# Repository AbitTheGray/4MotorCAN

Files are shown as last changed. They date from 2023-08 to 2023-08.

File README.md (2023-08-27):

# 3D Printer 4-Motor Board (CAN-bus Device)

This is a hobby project to create 3D Printer board to allow either control of all 4 motors (XYZ + Extruder) or 4 motors per axis.

The brain is [RP2040](https://www.raspberrypi.com/products/rp2040/) (can be flashed using USB-C connector) and has [TMC5160](https://www.trinamic.com/products/integrated-circuits/details/tmc5160/) as its muscle.
All the power and commands are provided by [CAN bus](https://en.wikipedia.org/wiki/CAN_bus) [Molex Micro-Fit 3.0 connector](https://www.molex.com/en-us/products/connectors/wire-to-board-connectors/micro-fit-connectors).
If you do not want to use CAN bus, you must provide 24V and GND on the connector and connect USB-C to your controller.

I have tried putting as many notes into the schematic as possible.
Buck converters and LDOs have their voltage limits close to the input pins (those are recommended limits, not absolute ones).

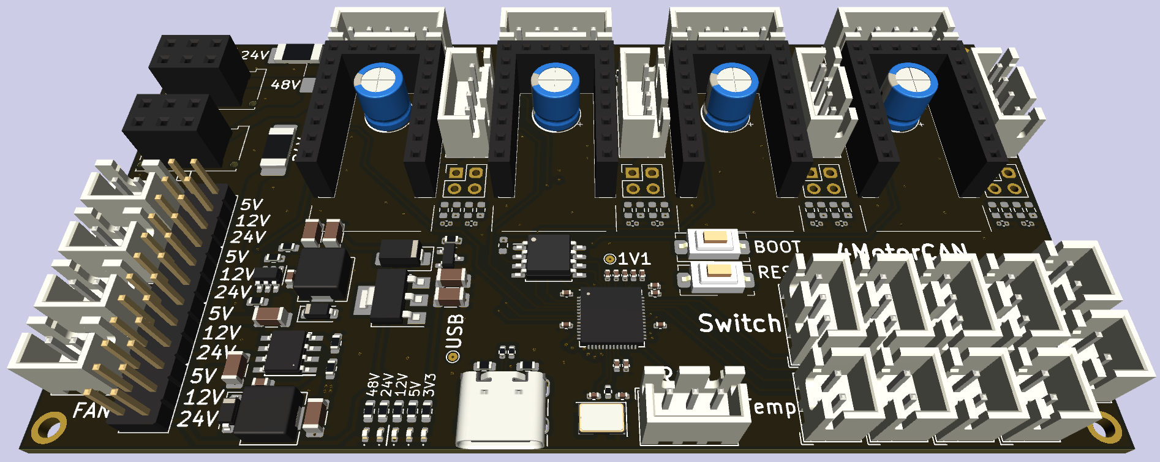
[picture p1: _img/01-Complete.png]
Fully-assembled PCB


*[Molex Micro-Fit 3.0](https://www.molex.com/en-us/products/connectors/wire-to-board-connectors/micro-fit-connectors) connectors are on the preview shown as 2x03 2.54mm/0.1" Pin Socket due to a missing 3D model.

## Features

- [CAN bus](https://en.wikipedia.org/wiki/CAN_bus) with power
  - 24V + 48V passthrough (48V optional, choose correct fuse orientation)
  - 5V signal
- 4x [TMC5160](https://www.trinamic.com/products/integrated-circuits/details/tmc5160/) to control motors (slotted PCB)
  - Encoder connector
  - Step LED (shows every step of the motor)
  - Optional direction switched (input, see TMC5160 documentation)
- 4x Limit Switch (endstop)
- RGB header (5V but signal is 3.3V)
- 4x 2pin Temperature sensor (resistor)
- 4x 2pin Fan control (5V / 12V / 24V) with 250mA fuse
- 2x Heating enable ("trigger", cannot power the heating)

### Warnings
- **This project was not yet tested. Use at your own risk.**
- This project uses RP2040 as if it was a 5V microcontroller.
  RP2040 is not officially 5V-tolerant but is reported by users to be able to process 5V input.
  And 3V output is 60% of 5V which should be enough for HIGH digital value of 5V devices.
- There is no overvoltage protection, do not turn axis motors too fast (manually)
  - Fan connectors have over-current protection (resettable fuse) in case of short circuit, but it will stop them from working
- Each motor has 3A max (total 12A) but [Molex Micro-Fit 3.0 connector](https://www.molex.com/en-us/products/connectors/wire-to-board-connectors/micro-fit-connectors) is rated only for 8.5A / 10.5A (depending on your source-of-truth) leaving only 2.125A / 2.625A per motor
    - This current limit is for the whole [CAN bus](https://en.wikipedia.org/wiki/CAN_bus)! The limit is least-rated connector in the network
    - [JST XH connectors](https://www.jst.com/products/crimp-style-connectors-wire-to-board-type/xh-connector/) should not esceed 3A.
- You should not power any heating through [CAN bus](https://en.wikipedia.org/wiki/CAN_bus) as power consumption can exceed safe limits for those connectors (and wires).

Keep in mind any current/temperature limits can be lower for higher-temperature environments (like fully boxed-in 3D printer).

## Limits and Power Consumption

| Component | Expected Max Current | Max Temperature |
|---|---|---|
| RP2040 (microcontroller) | 50 mA | 85 °C |
| W25Q128JVS (flash) | 4 mA | 85 °C (105 °C)  |
| TMC5160 (motor driver) | | 125 °C |
| Stepper motor | 3A (x4) | |

## Usage

Following usages are all theoretical based on hardware capabilities, none have been tested.

In case you do not want to use the 3mm pitch Molex connector for power, you can use the 3 pads in top-left corner to solder your wires directly to the PCB.
This is not recommended as it will usually skip fuse for motors (unless you use 24V for motors using `F103`).

### 3D Printer Board

This board can be used as a main 3D printer board as it has everything required for a basic printer (4 motors, limit switches, temperature sensors, heating triggers).

### CAN/USB Device

This device can be controlled using either [CAN bus](https://en.wikipedia.org/wiki/CAN_bus) or USB.
Having 4 motors and several input/output connectors, you can control most/all of the 3D printer from single CAN device.
In case of multiple motors per axis, you may need multiple devices (this board was primarily designed to control 4 Z-axis motors using single controller over CAN).

## Fabrication

DNP (Do Not Place/Populate) symbols are also removed from "Component Position" output.
The same applies to all connectors as those are not recommended/possible for automatic soldering.

You can save some money by replacing `R602`+`D601` by `R601` (and equivalent for `R701`,`R801` and `R901`) and omitting `R101`-`R105` and `D101`-`D105` (power indication LEDs).

### Problems

- No equivalent for `C201`/`C202` currently available
- No THT connectors in Component Placement files
  - 10x 2pin JST XH
  - 5x 3pin JST XH
  - 4x 4pin JST XH
  - 4x 5pin JST XH
  - 2x [Molex Micro-Fit 3.0 connector](https://www.molex.com/en-us/products/connectors/wire-to-board-connectors/micro-fit-connectors)
  - 2x12 2.54cm/0.1" Pin Header
  - 4x 4pin 2.54cm/0.1" Pin Header
  - 8x 8pin 2.54cm/0.1" Pin Header

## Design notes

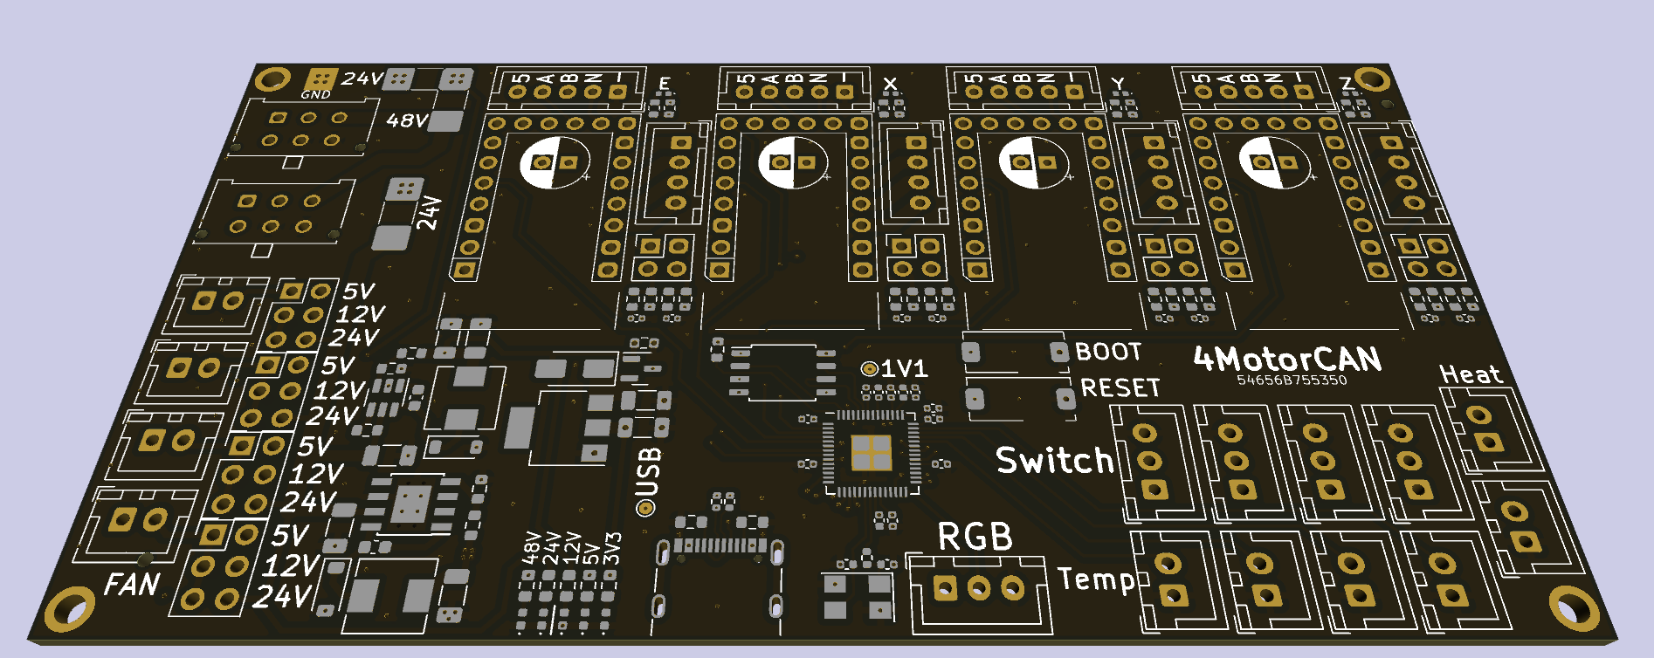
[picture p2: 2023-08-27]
_img/03-PCB.png

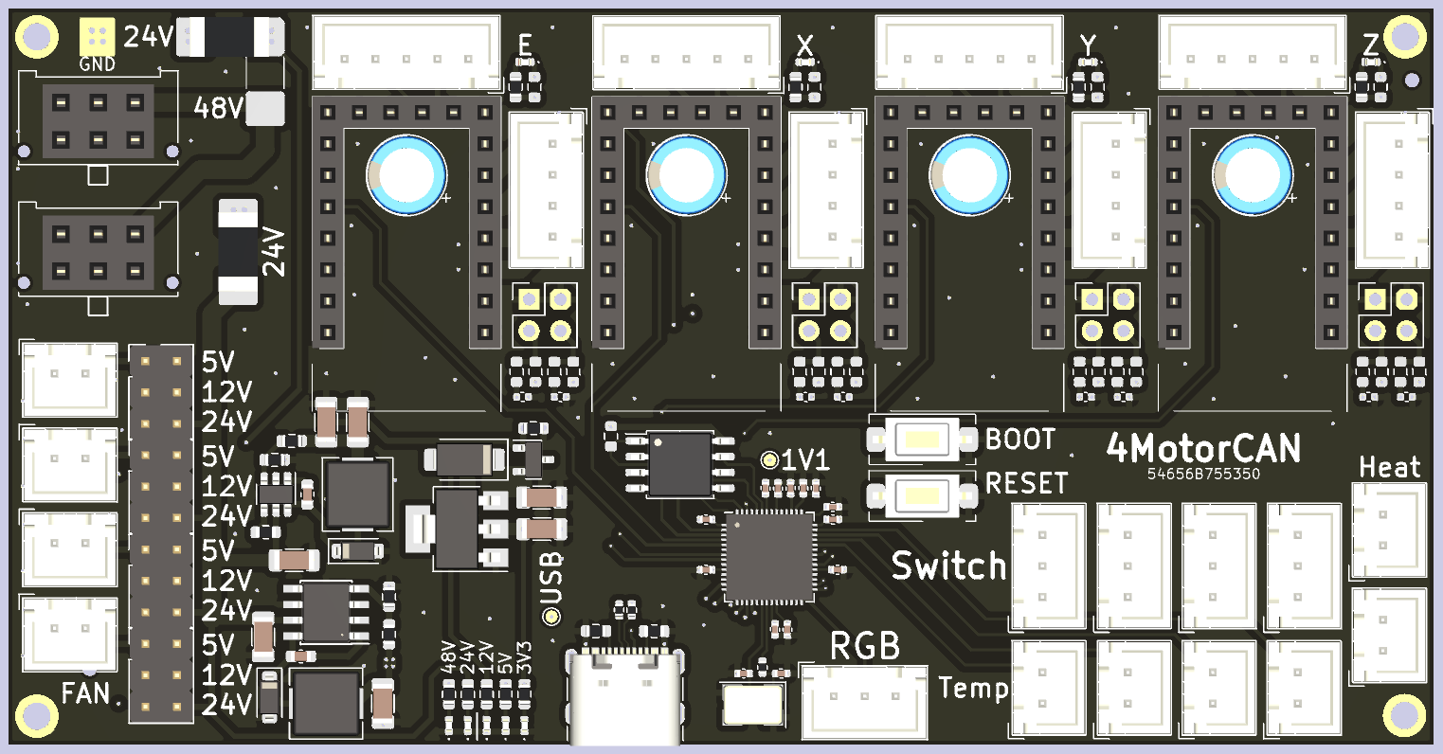
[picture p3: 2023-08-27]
_img/Topdown.png

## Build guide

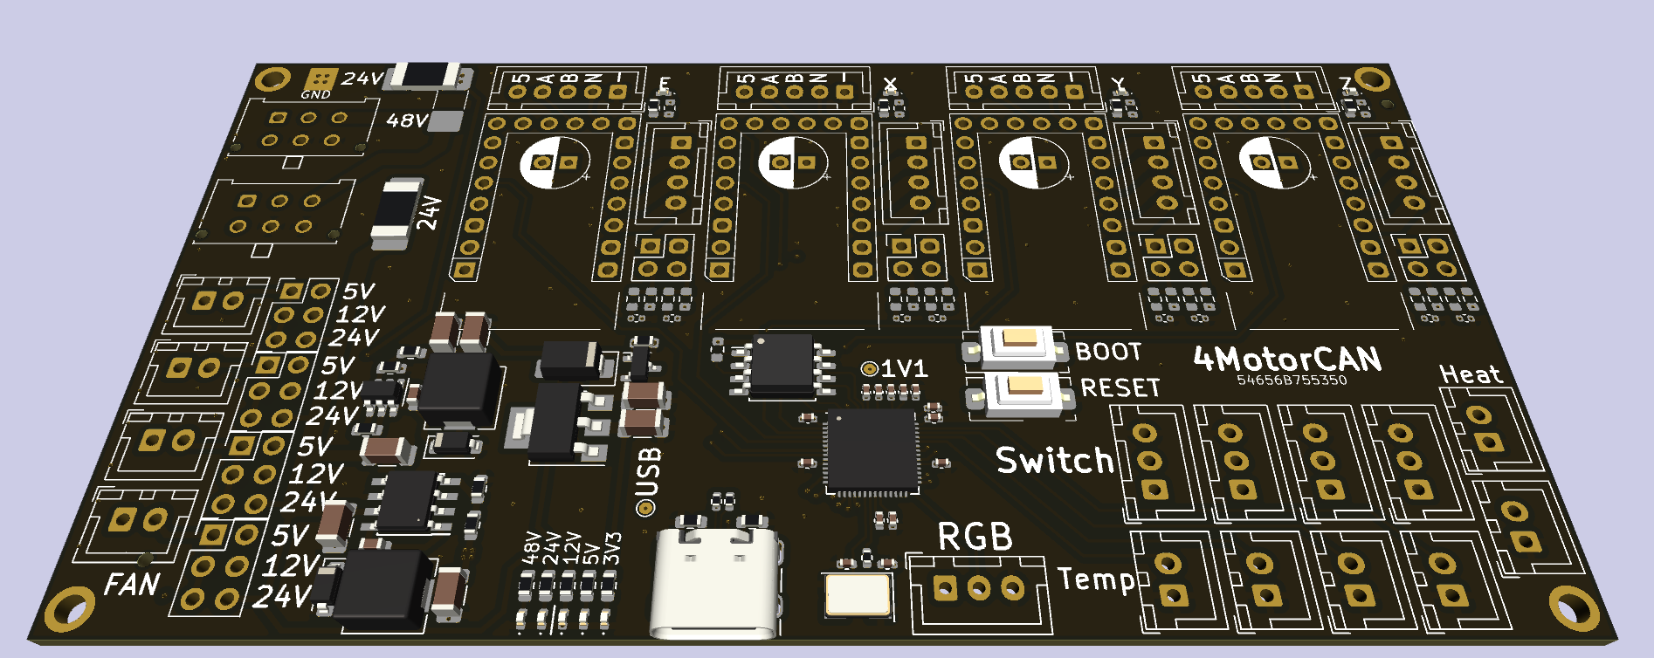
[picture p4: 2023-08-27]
_img/02-Assembly.png

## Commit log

2023-08-18 Initial raw draft
    [Can3DPrinter4Motor.kicad_pcb, Can3DPrinter4Motor.kicad_sch, Fans.kicad_sch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]
2023-08-19 Assigning a lot of values to components Change MOSFETS for different (correct) ones Copy Motor1 to Motor2-4 Guess max current per voltage on PowerSupply schema
    [Can3DPrinter4Motor.kicad_sch, Fans.kicad_sch, Microcontroller.kicad_sch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]
2023-08-19 Complete schematics Assign every value (very few exceptions) Change TCM5160 from on-board to separate module Add fuses Add power supplies (LDO + 2x buck converter)
    [Can3DPrinter4Motor.kicad_pcb, Can3DPrinter4Motor.kicad_sch, Fans.kicad_sch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]
2023-08-19 WIP PCB placement, minor fixes
    [Can3DPrinter4Motor.kicad_pcb, Can3DPrinter4Motor.kicad_sch]
2023-08-19 More PCB placement, fix 48V for Motors
    [Can3DPrinter4Motor.kicad_pcb, Microcontroller.kicad_sch, Motor1.kicad_sch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]
2023-08-22 Finish wiring PCB
    [4MotorCAN.kicad_pcb, 4MotorCAN.kicad_sch, Fans.kicad_sch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]
2023-08-27 Finish PCB, documentation
    [4MotorCAN.kicad_sch, Microcontroller.kicad_sch, Motor1.kicad_sch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]
